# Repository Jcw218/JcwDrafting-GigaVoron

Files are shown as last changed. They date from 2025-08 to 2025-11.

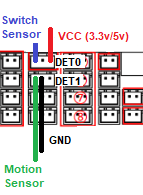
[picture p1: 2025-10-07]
BTT_smart_filament_detection_module_install_guide/filament detector.png

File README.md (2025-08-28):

# JcwDrafting-GigaVoron
Modifications to the Orangestorm Giga to improve its usability, Modifications and reliability. 
                                            WARNING!!! 
With the exception of the Print head; these modifications will not work with the original manufacturers motherboard or firmware.

Please be make sure you know the limits of your machine, the included data package is for the following parts:
- Octopus Pro V1.1 & V1.0 (F446 and H723)
- Raspberry Pi 4
- EB SB2209 CAN (RP2040 and STM32G0B1)
- BTT Eddy Duo (CANBUS Capable)
- BTT Pi V1.2
- Knomi 2 (important due to bed leveling integration. Bed level will not work without it. Modify the firmware to suit if it's not included)

To Install Klipper using the octopus pro as a CANBUS bridge follow Esoterical CANBUS guide here: https://canbus.esoterical.online/mainboard_flashing

Included in this data pacakge: 
- Apapter plate Step files for Stealth Burner and other hotend attachements
- Klipper install package to suit octopus pro, Raspberry pi, Eddy, BTT SB2209, SB2240, 
- Firmware for Octopus Pro and Raspbarry Pi motherboard upgrade
- Config for Octopus Pro motherboard upgrade and Stealthburner printer head
- Additional code and details for Obico Monitoring
- Adapter plate for nema 23 X axis upgrade
- Coming soon: Oem 10.1" TJC Touch Screen Firmware package for integration with new upgrades

Feel like buying me a coffee?

https://buymeacoffee.com/JakeCharles

bmc_qr

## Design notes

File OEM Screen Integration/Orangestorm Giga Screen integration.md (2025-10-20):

####################################################################################
### Machine type: JcwGiga
### Current configuration version: VBeta
### Date：2025-10-20
### OEM SCREEN INTEGRATION WITH OPEN SOURCE KLIPPER INSTALL
### OEM Stepper Motors and Stock Stepper Drivers
####################################################################################

This is a guide on how to configure the OEM SCREEN to operate with new board hardware running a newer version of klipper. This being said, this guide can also be applied to newer versions of klipper installed on the OEM board running a MKS pi

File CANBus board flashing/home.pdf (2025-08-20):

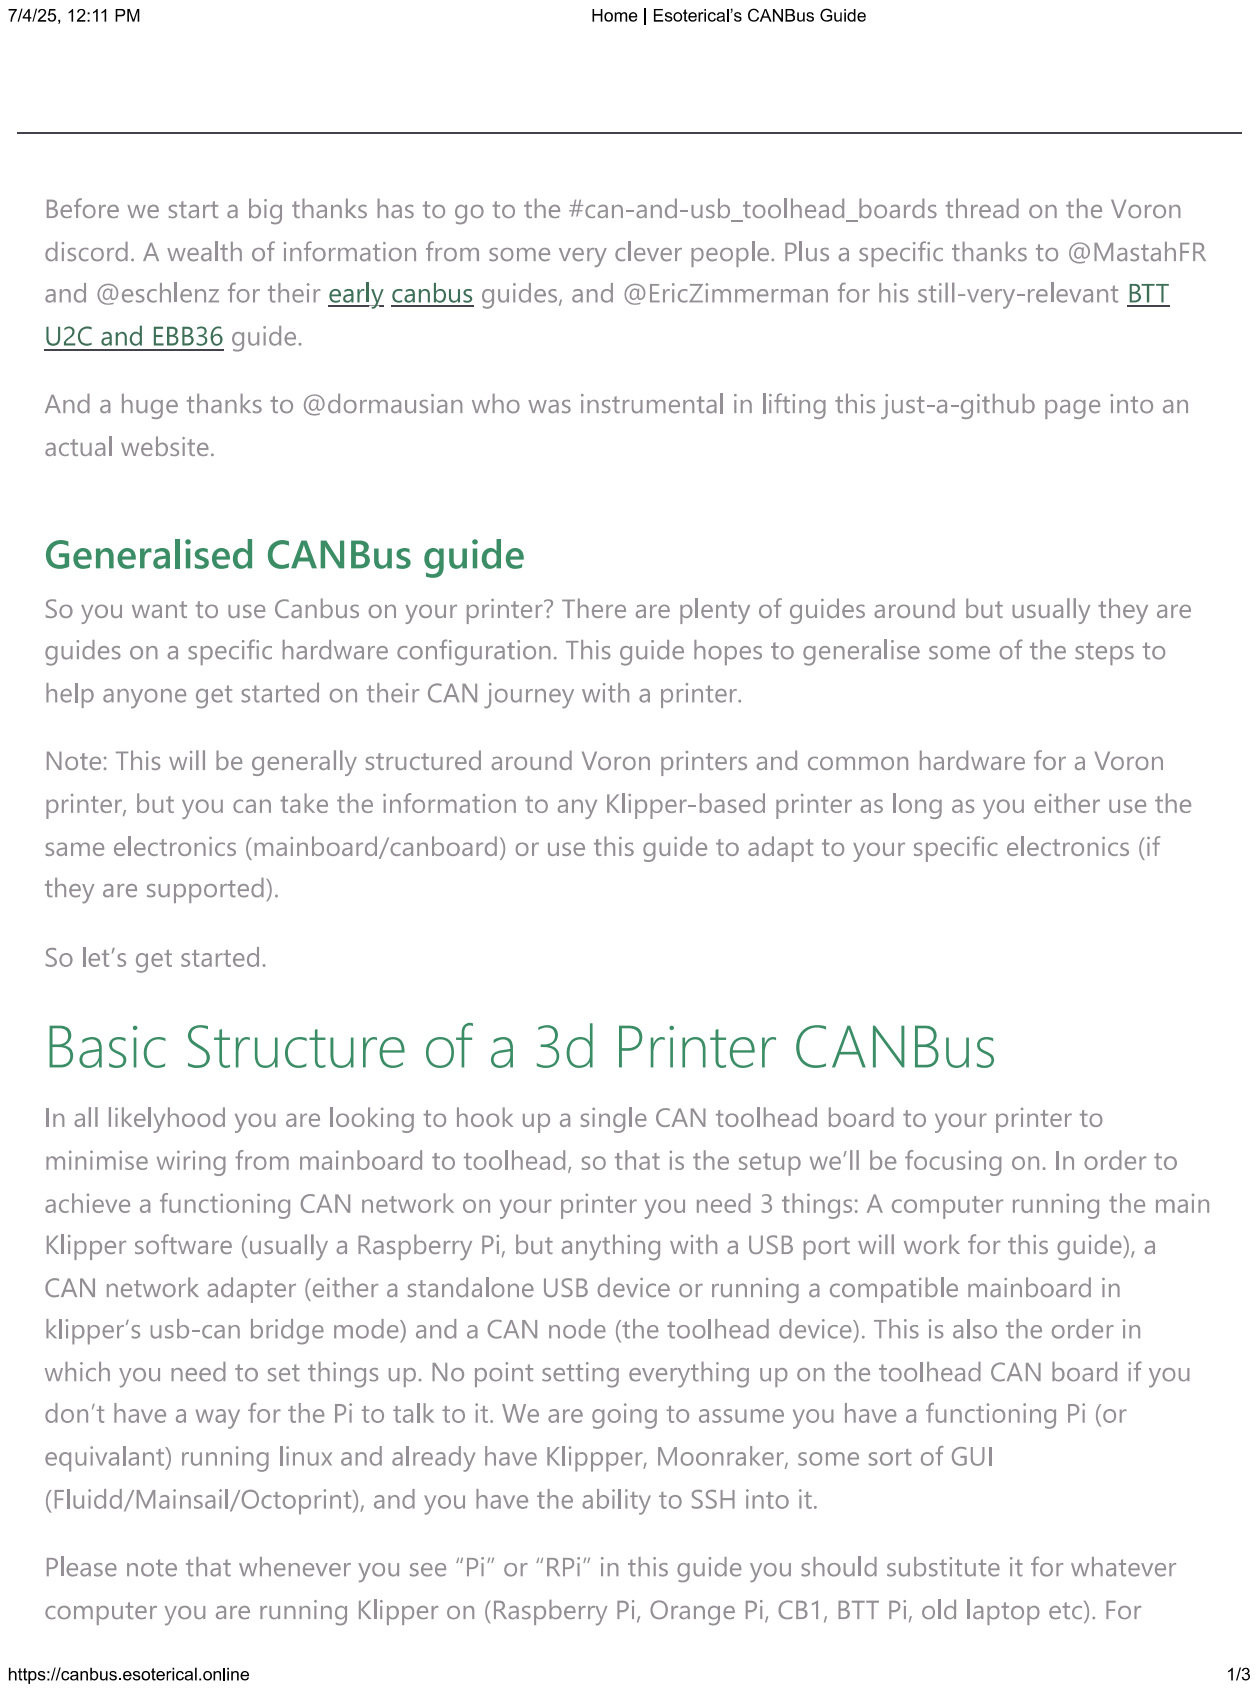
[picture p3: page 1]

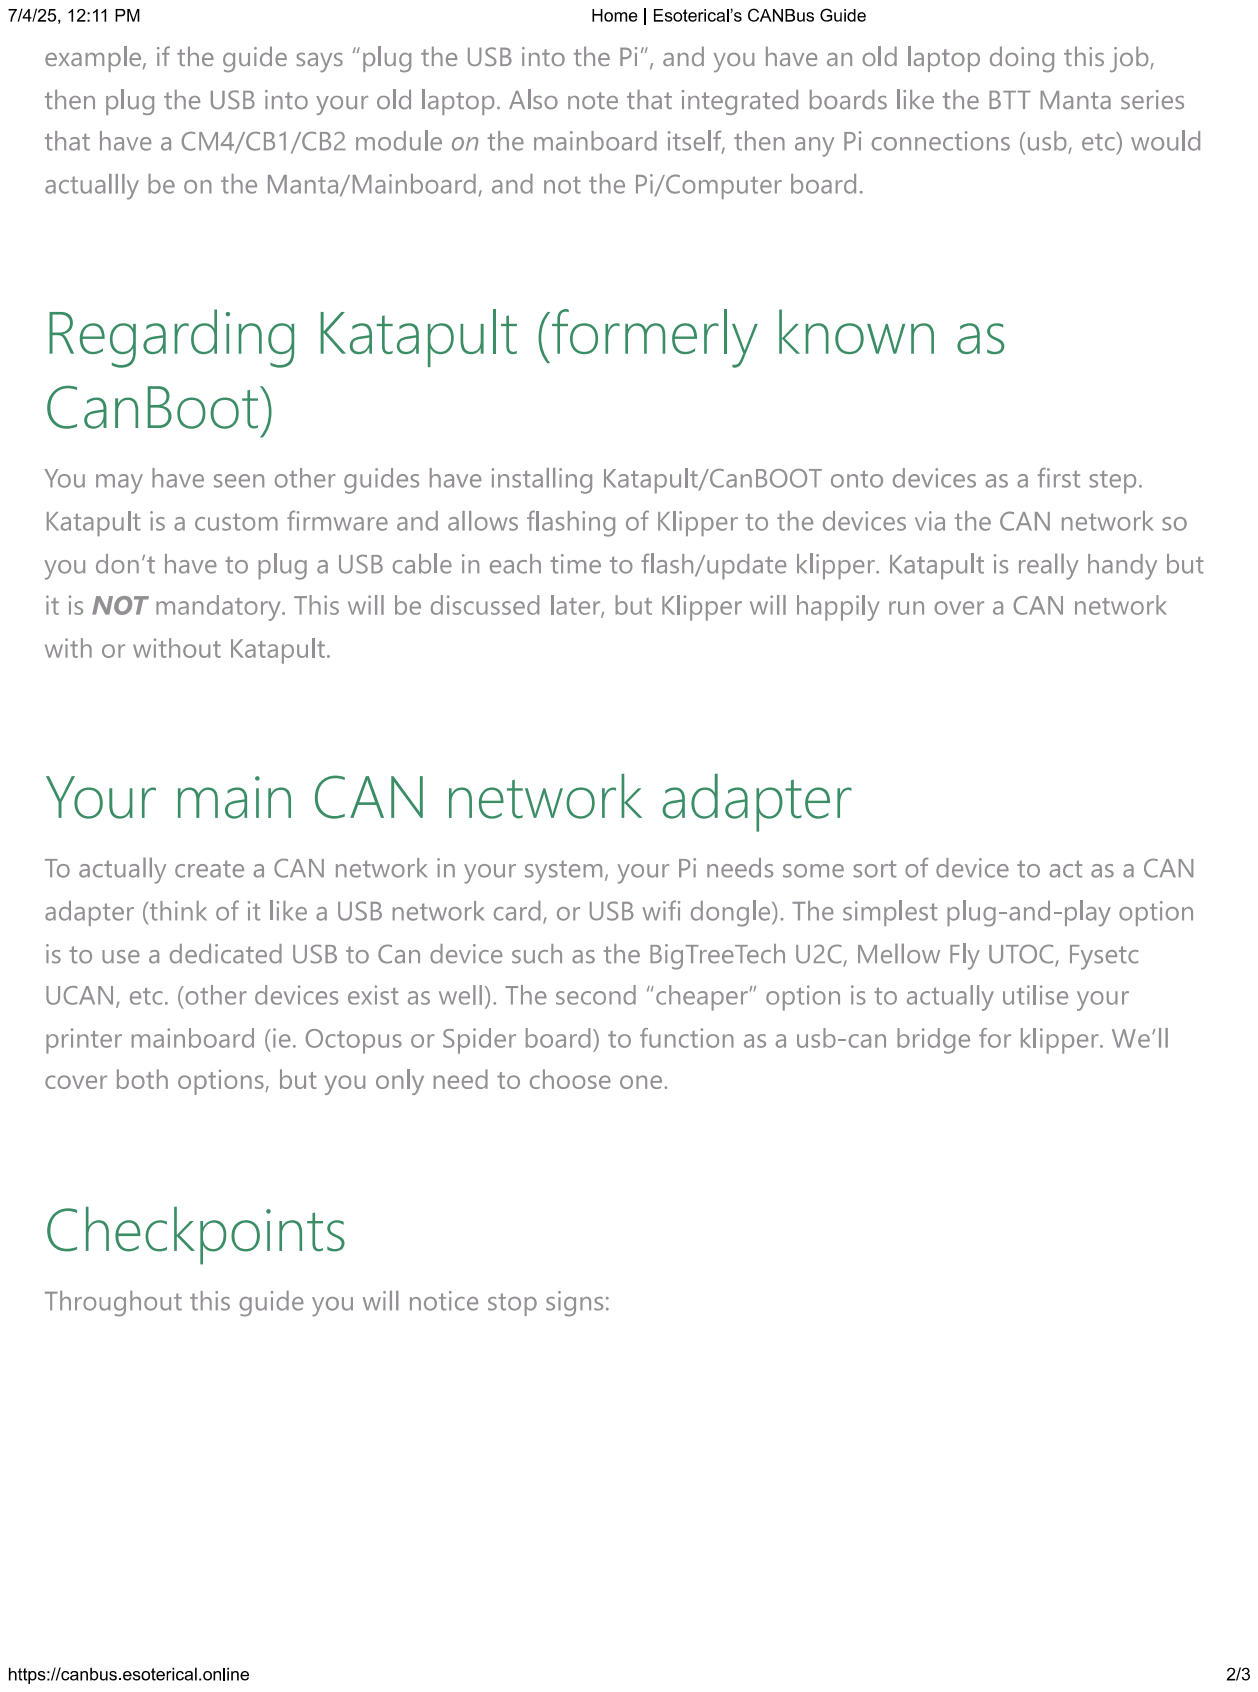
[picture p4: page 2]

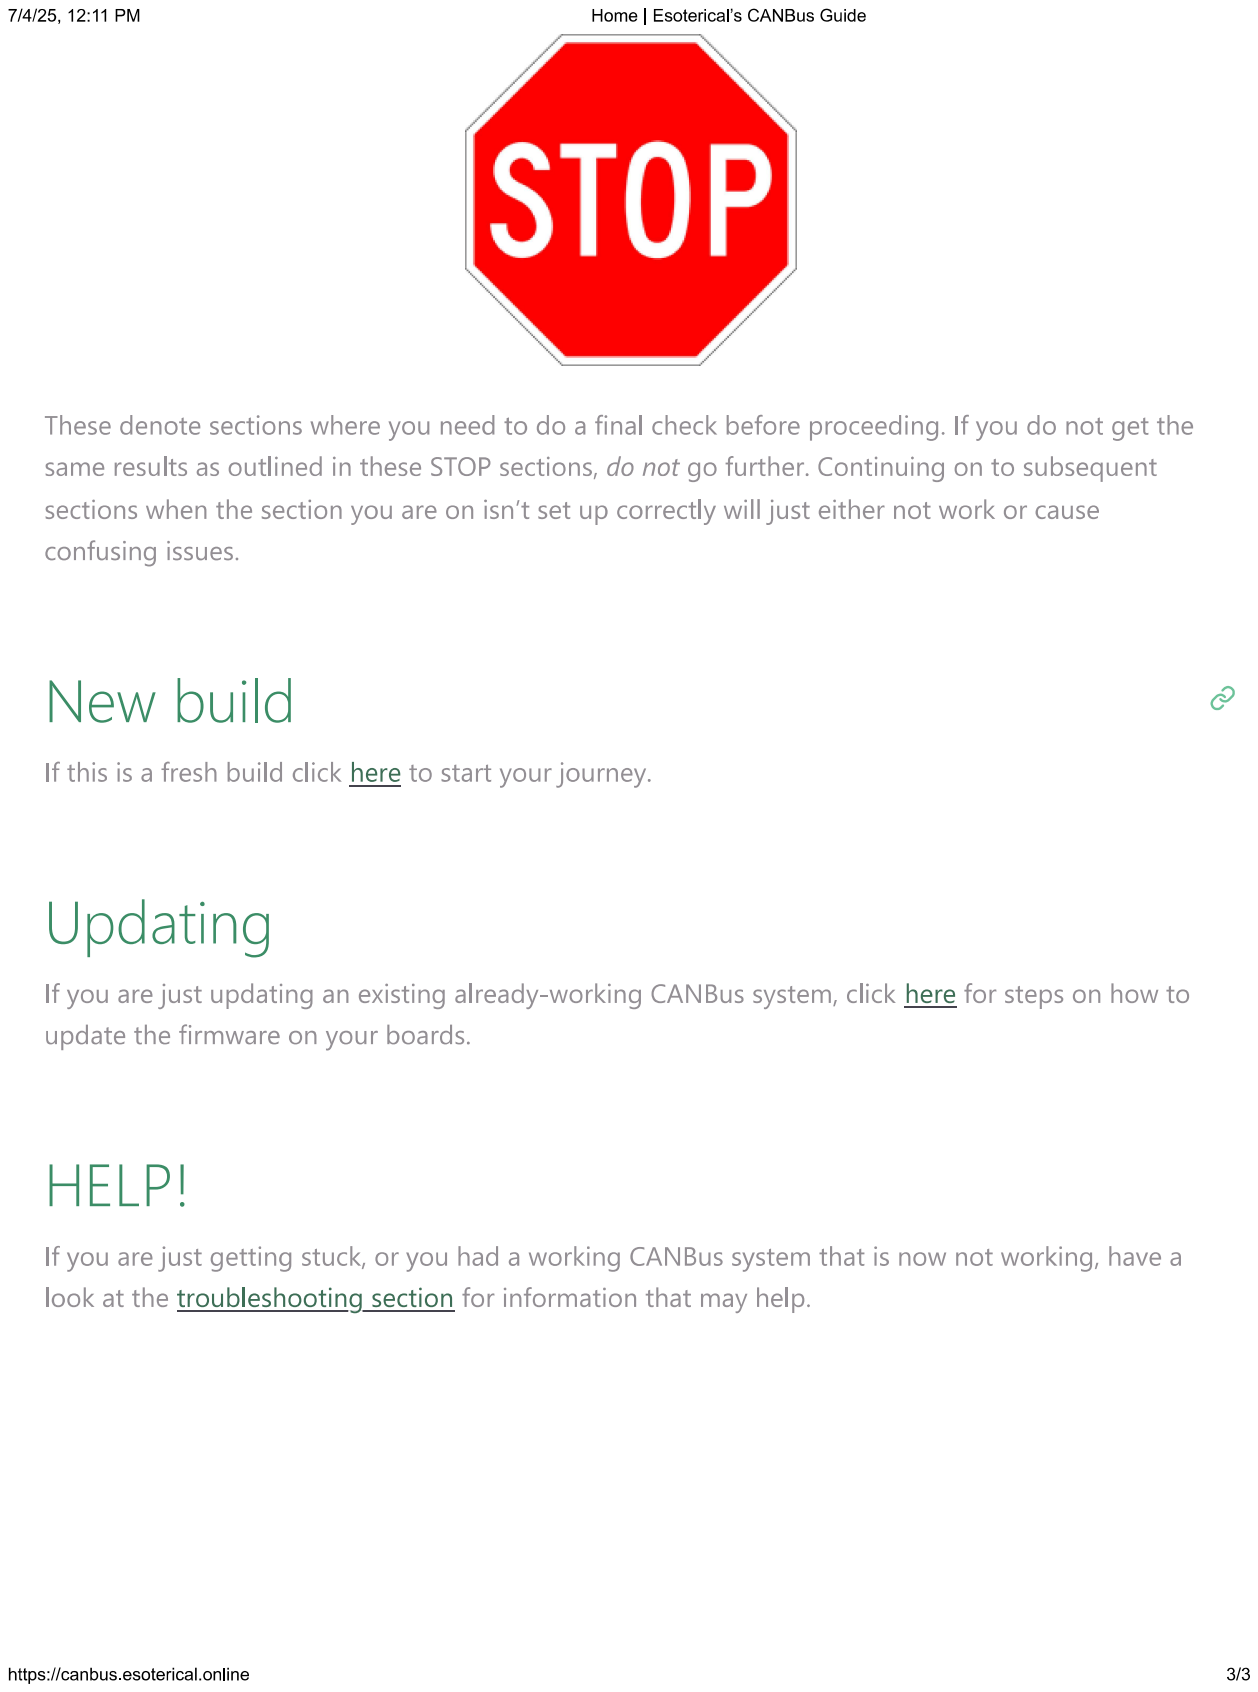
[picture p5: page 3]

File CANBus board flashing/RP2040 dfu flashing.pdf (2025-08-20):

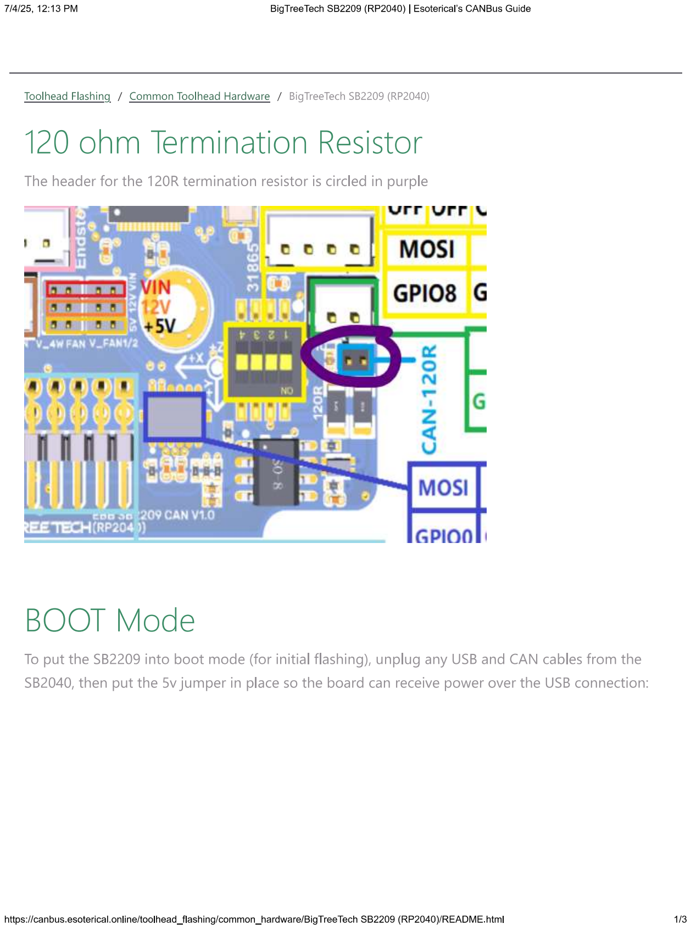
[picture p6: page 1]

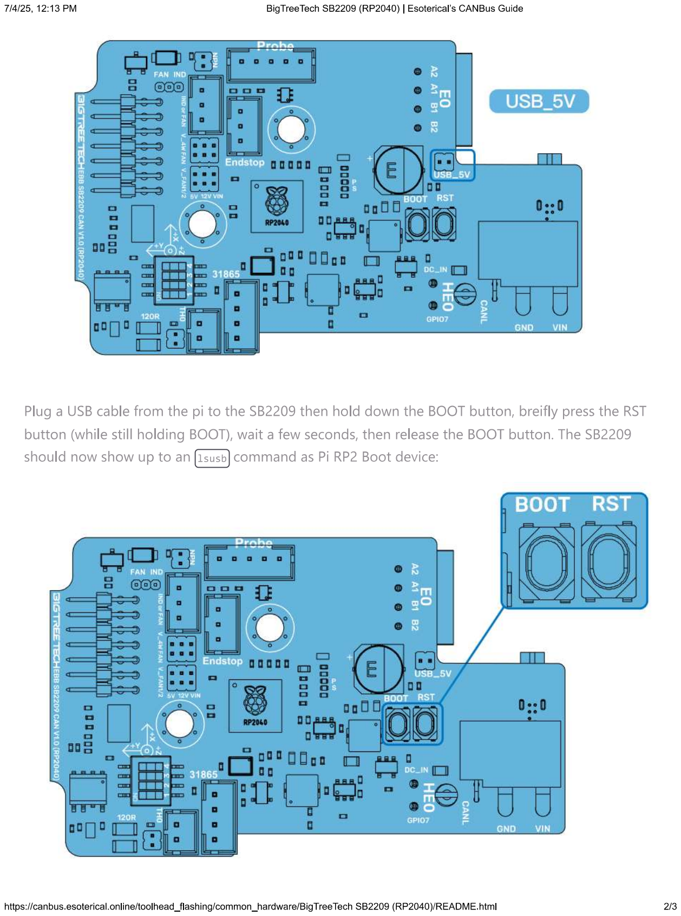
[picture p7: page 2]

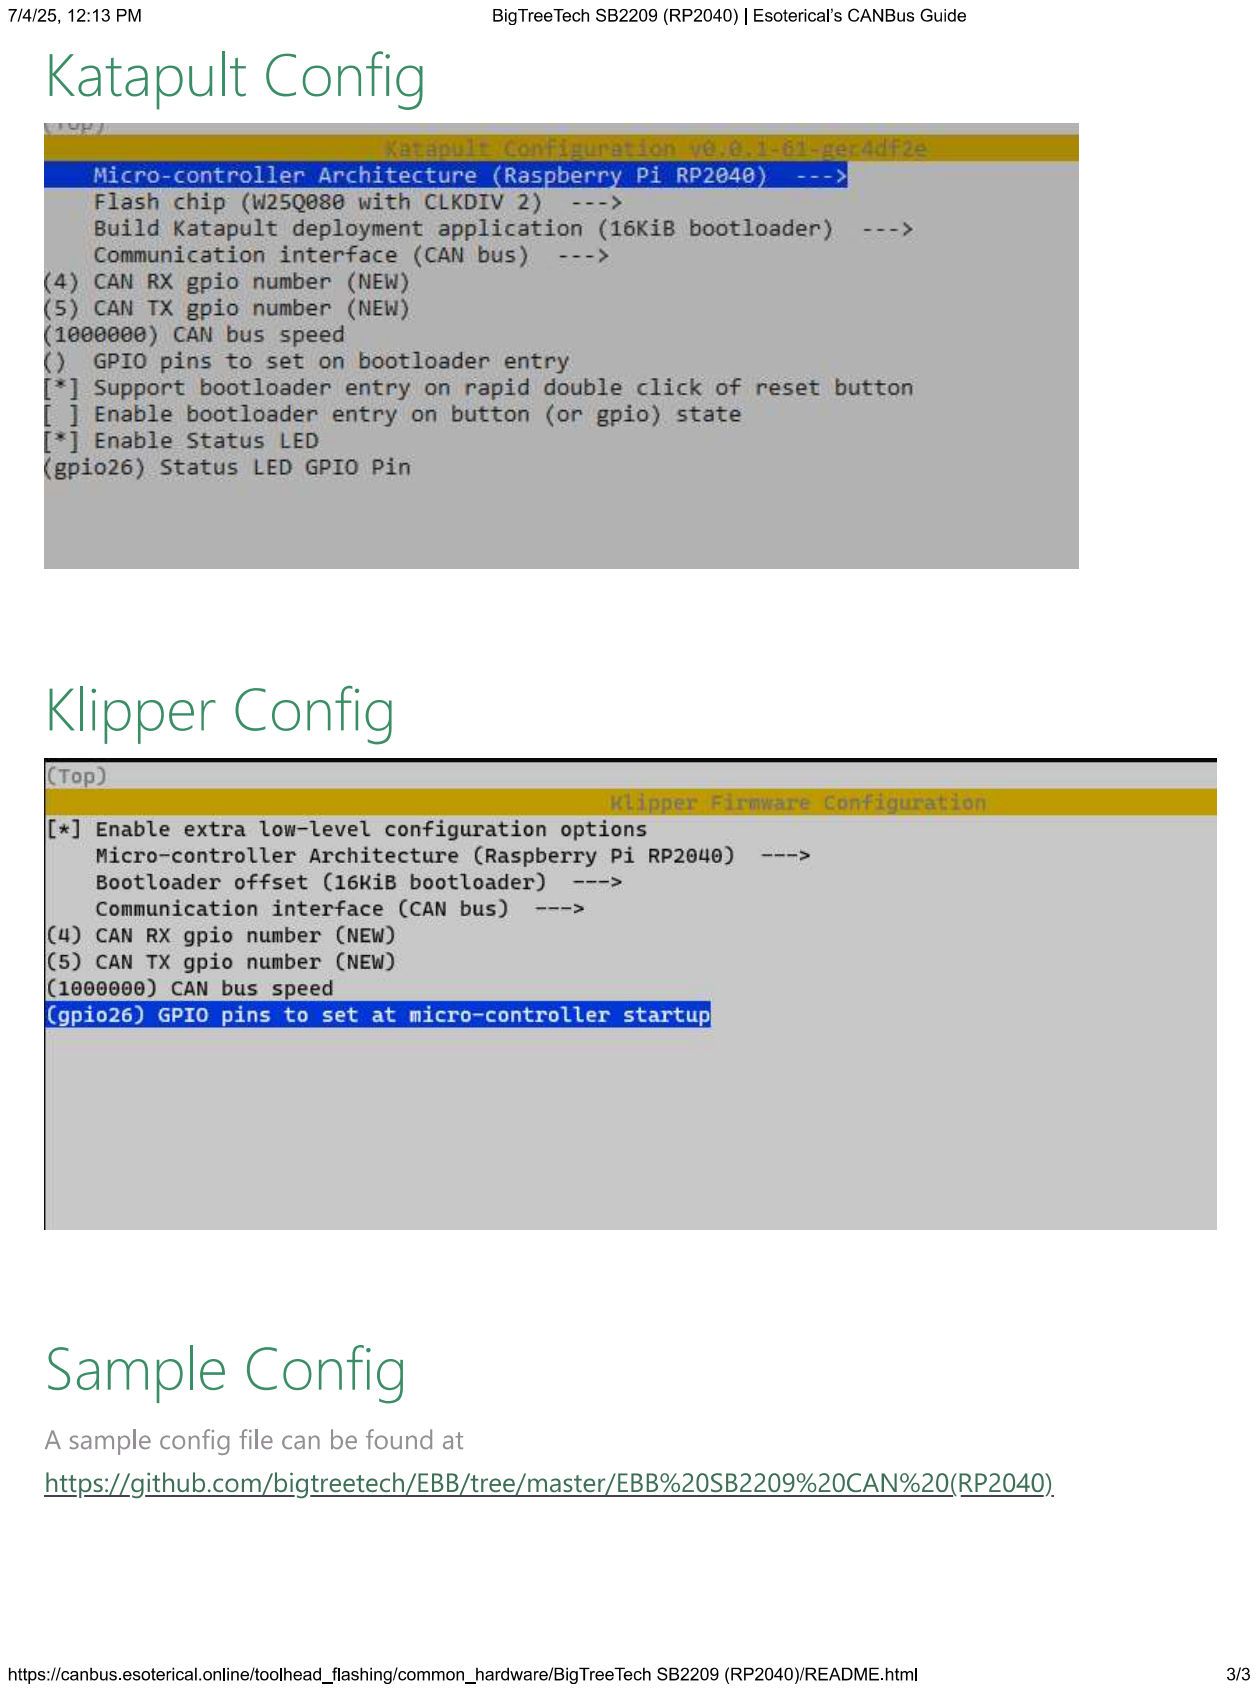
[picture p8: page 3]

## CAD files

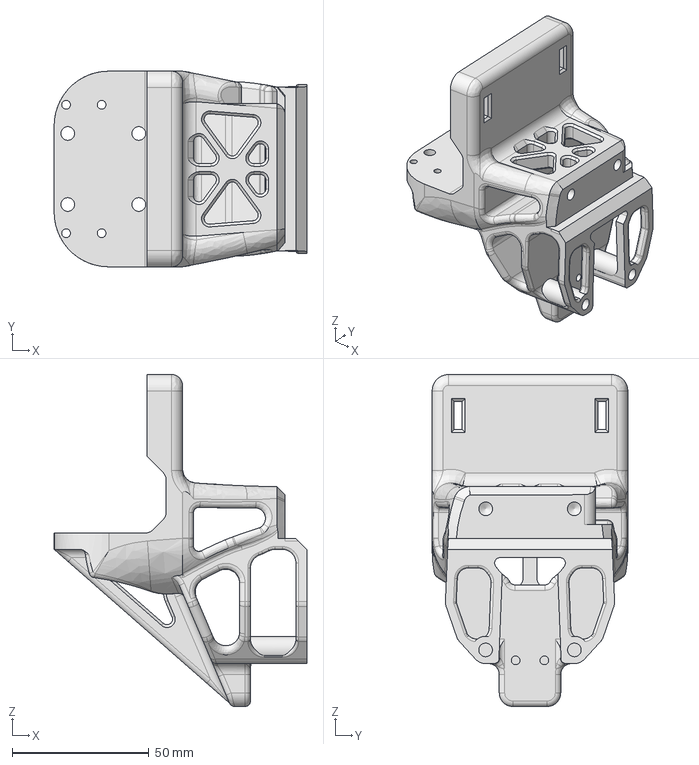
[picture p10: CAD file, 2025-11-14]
3D Print File - Dragon ACE SB with Extension/Full Printhead unit.stp
92.5 x 71.6 x 121.5 mm

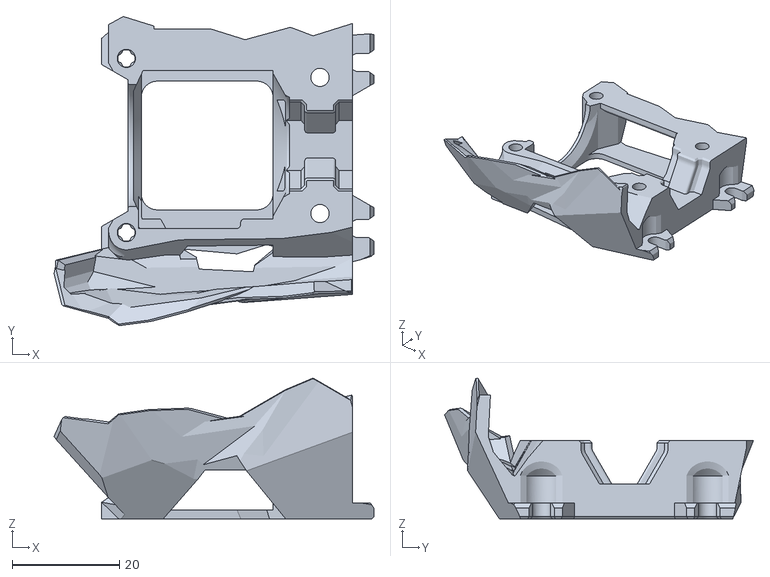
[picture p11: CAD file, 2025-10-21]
3D Print File - Bambulabs SB/BambuLabs SB Back.stl
59.7 x 57.7 x 26.3

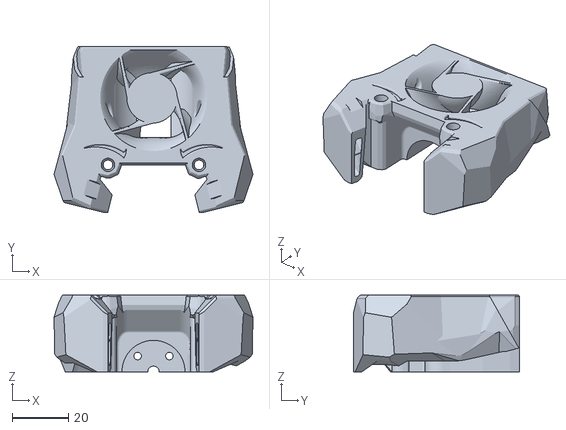
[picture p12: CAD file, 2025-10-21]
3D Print File - Dragon Ace SB/Dragon ACE SB Front.stl
71.1 x 59.1 x 27.4

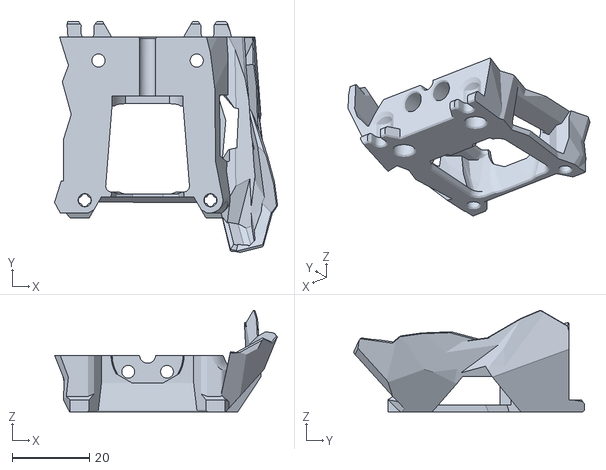
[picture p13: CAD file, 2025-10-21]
3D Print File - E3D Revo SB/E3D Revo SB Back.stl
57.7 x 59.7 x 26.3

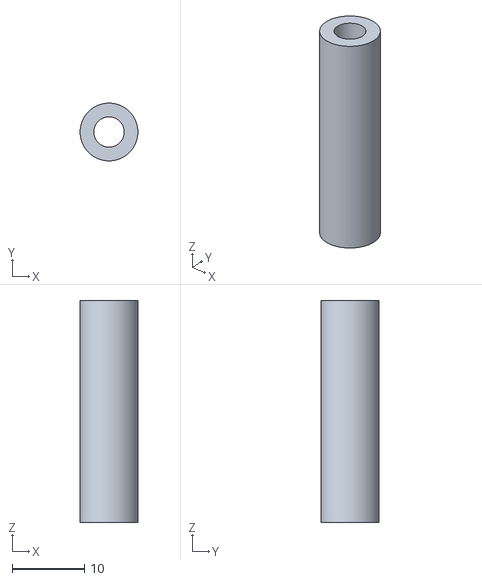
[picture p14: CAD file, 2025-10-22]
3D Print File - Giga Modifications/Bed Leveling Bushes.stl
8.00 x 8.00 x 30.7

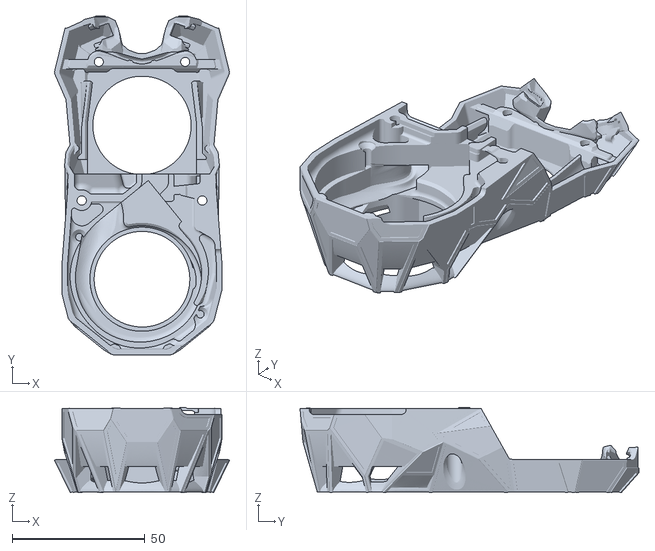
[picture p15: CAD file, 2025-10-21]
3D Print File - SB Components/Jcw Drafting Stealth Burner Face.stl
66.0 x 127.7 x 32.1

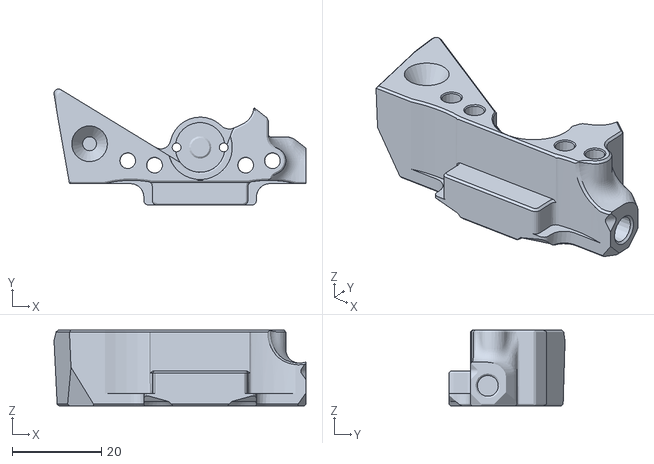
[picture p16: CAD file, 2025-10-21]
3D Print File - SB Galileo V2/SB Galileo Base Hinge Retainer.stl
56.4 x 26.0 x 17.0

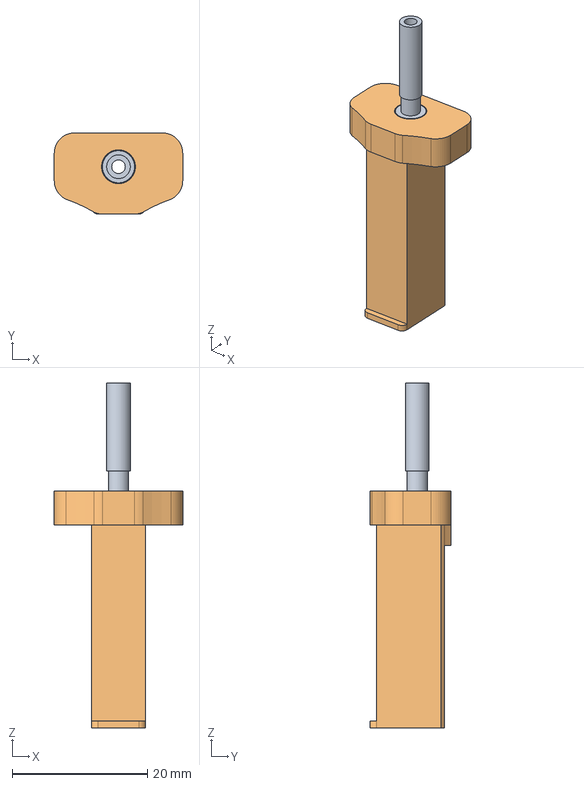
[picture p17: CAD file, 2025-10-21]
Stock Giga Print Head 3D models/Giga Extruder hotend.stp
19.0 x 12.0 x 51.0 mm

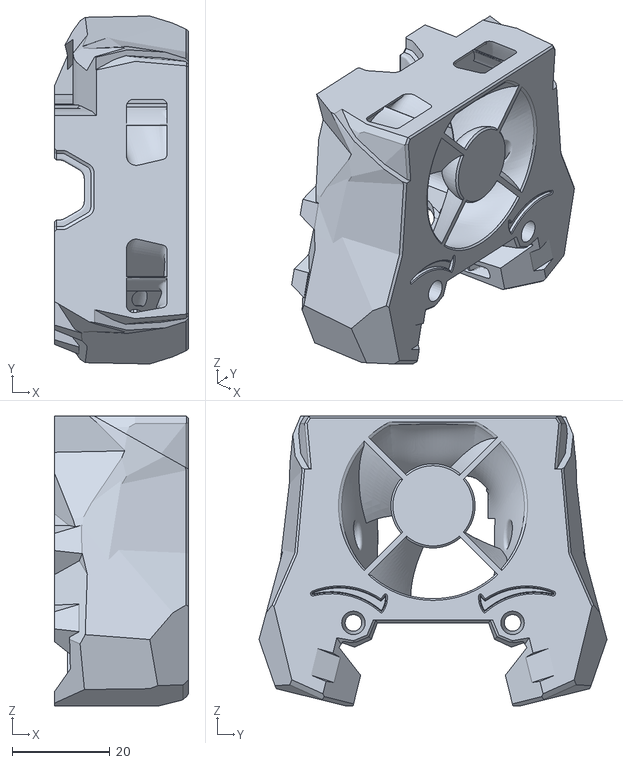
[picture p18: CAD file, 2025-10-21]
3D Print File - Bambulabs SB/Bambulab SB Front.stl
27.4 x 71.1 x 59.1

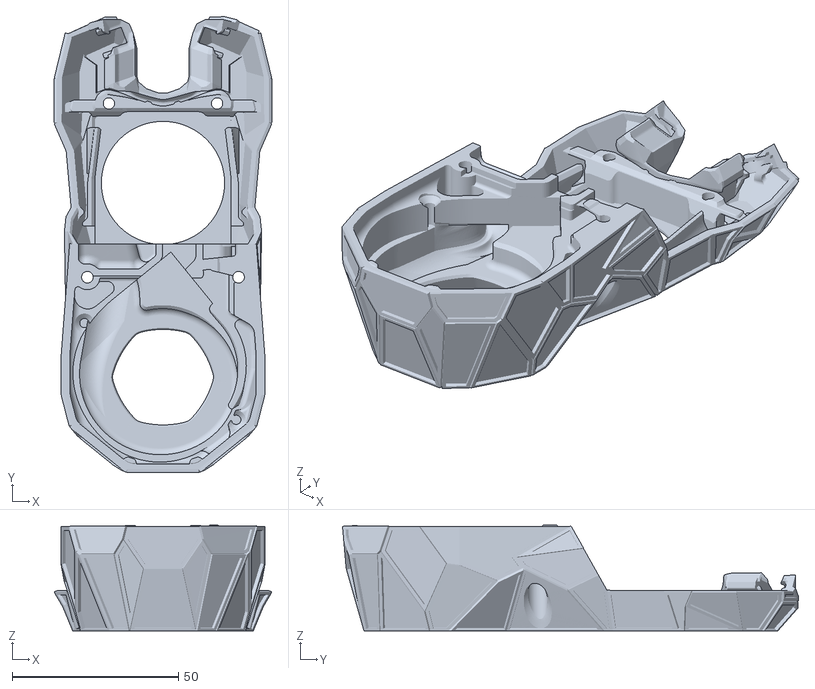
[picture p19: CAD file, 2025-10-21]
3D Print File - Dragon ACE SB with Extension/Dragon Ace SB with Extension Face.stl
65.3 x 137.0 x 31.8

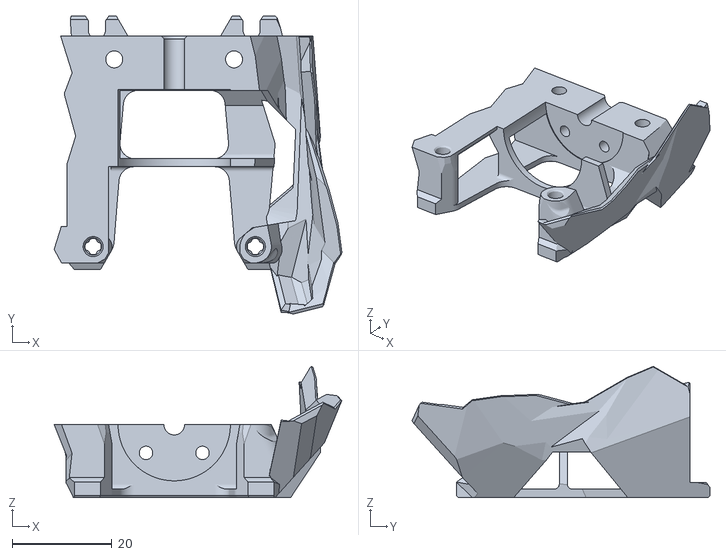
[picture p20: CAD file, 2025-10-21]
3D Print File - Dragon Ace SB/Dragon ACE SB Back.stl
57.7 x 59.7 x 26.3

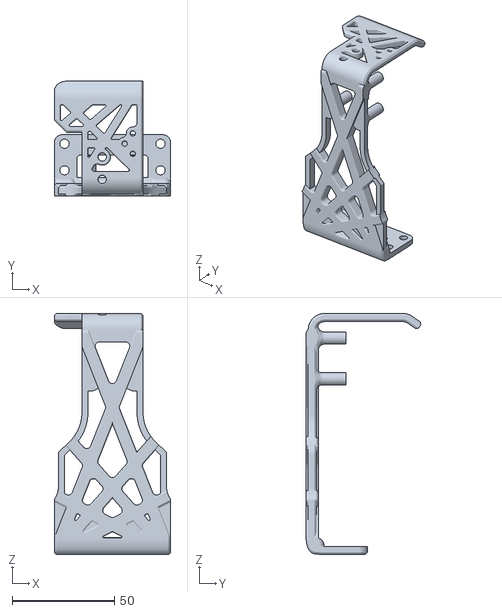
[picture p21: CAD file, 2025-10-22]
3D Print File - Giga Modifications/Giga Extruder Canbus cable chain bracket.stl
57.0 x 56.2 x 118.0

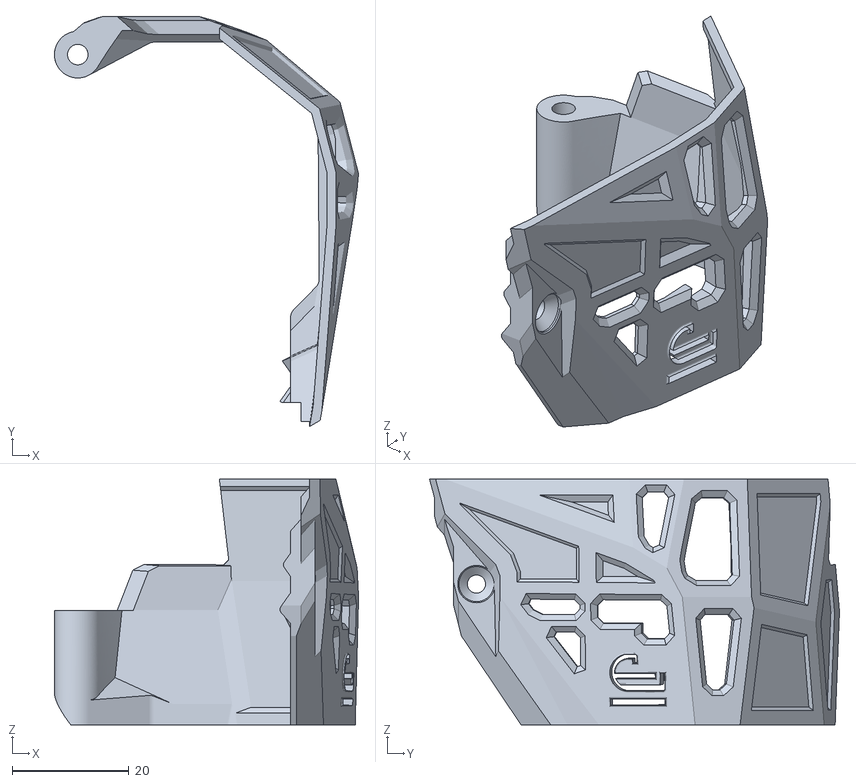
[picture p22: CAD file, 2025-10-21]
3D Print File - SB Components/SB Electronics Shroud.stl
52.1 x 70.2 x 42.1

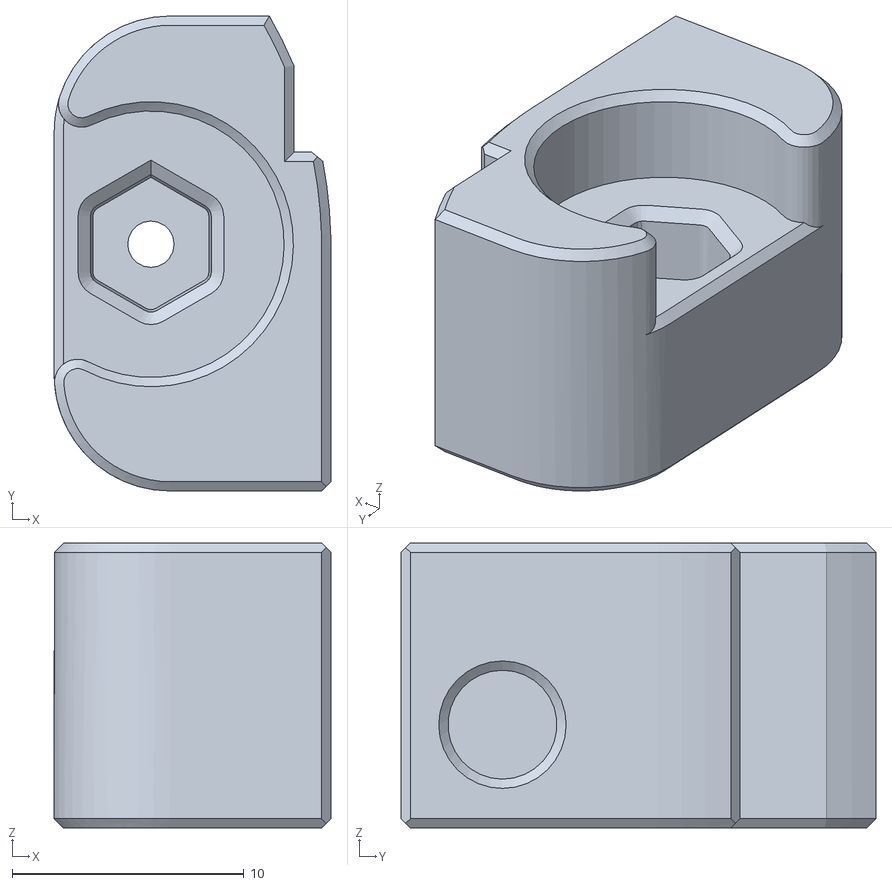
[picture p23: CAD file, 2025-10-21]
3D Print File - SB Galileo V2/SB Galileo Extruder Bearing Retainer.stl
11.9 x 20.5 x 12.3

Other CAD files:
3D Print File - OG Dragon SB/Dragon SB Back.stl
3D Print File - E3D Revo SB/E3D Revo SB Front.stl
3D Print File - OG Dragon SB/Dragon SB Front.stl
Stock Giga Print Head 3D models/Level Sensor v3.stp
3D Print File - Bambulabs SB/BambuLabs SB Adapter.stl
3D Print File - Dragon ACE SB with Extension/Dragon ACE SB with Extension Back.stl
3D Print File - Dragon ACE SB with Extension/Dragon ACE SB with Extension Front.stl
3D Print File - Giga Modifications/Giga Extruder Linear Rail Plate.stl
3D Print File - Giga Modifications/Giga Frame Corner Brace with enclosure mount hole.stl
3D Print File - Giga Modifications/Giga Z axis Bushing for Calibration.stl
3D Print File - Giga Modifications/Nema17 to Nema23 x axis adapter.stl
3D Print File - Giga Modifications/Octopus Pro Motherboard Mounting bracket.stl
3D Print File - Giga Modifications/PI Mouting bracket.stl
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

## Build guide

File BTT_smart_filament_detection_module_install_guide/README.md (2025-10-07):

## Guide to Installing the BTT smart filament detection module to the original Elegoo Orangestorm Giga Motherboard V3
558768329_10235050453376534_4001759081982270624_n

1. Firslty, figure out where you want the sensor. If the sensor is too far away from the print head, it may trigger more regularly than if the sensor was placed closer to the print head.


2. If you are using the DET0 and DET1 headers at the back of the printer; make sure both headers are properly pluged into the headers on the motherboard. You may need to run another cable from the DET1 header to the DET1 on the motherboard.

  558884123_10235066154769059_1636835637515836587_n
  557631873_10235066176769609_8913204024433743418_n

4. The BTT smart filament sensor should be wired as per the following image:
  filament detector

5. Locate the IP address of your printer.
  

6. Enter the IP address of your printer into google chrome and hit enter. You'll be greeted by the Fluidd Interface.
  

7. Locate the Configuration tab on the left side of the Interface.
  

8. Double left click on the printer.cfg file

9. scroll down and find the following entry.
  

10. type # to uncomment this code or delete this code and then type in the following instead:
  

11. PD5 is the incorrect swtich_pin id. located you pins.h file and determine the right ID to enter in the place of PD5. The encorder pin detects if the filament is running through the switch and is very handy to determine whether your first layer is accurate or whether you have a clogged nozzle.

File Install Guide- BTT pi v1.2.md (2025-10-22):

####################################################################################
### Machine type: JcwGiga
### Current configuration version: VBeta
### Date：2025-9-11
### BTT Pi V1.2 - Octopus pro V1.1 - EBB SB2209-RP2040
### OEM Stepper Motors and Stock Stepper Drivers
####################################################################################

This is a Tutorial on how to install this repositories operating system to a BTT pi V1.2 and configure it for the Elegoo Orangestorm Giga manually

Step 1:
Ensure that your Giga is turned off and isolated from power. You may also want to wait a day to ensure that the capacitors are drained of electricity and are safe to touch.

Step 2:
Removing the Mother board cover panel on the right side of the machine as detailed in the images below:

  - Ensure that your print head is at the z heigth of 300-500 and out of the way so that the motherboard panel can be removed. You may need to manually home first and then set the z height to 300 or 500.
    
    
    
  - Loosen the 2 screws fixed by the PEI limit block at the right front and back side of the printer using a 2.0mm Allen wrench to remove the PEI limit block.
    
    
  
  - Disconnect the ribbon cables from the rear adapter board located on the right side of the printer.
    
    
  
  - Use a 2.0mm Allen wrench to loosen the 8 screws securing the power supply cover.
    
    

  - Slide the power supply cover downward towards the heated bed, then lift the outer edge of the cover to remove it.
    
    

Step 3:
Removing the Motherboard and marking the wires as per the images below:

  - Use cable ties or label paper to mark the ribbon cables that lack original markings, ensuring they correspond to the port names on the motherboard.
    
    

    Motherboard sch

  - Disconnect all ribbon cables from the ports on the motherboard. Use a 2.0mm Allen wrench to loosen the 4 screws securing the motherboard, and remove the old motherboard.

    

Step 4:
Install Klipper onto Big Tree Tech pi V1.2, Octopus Pro V1.1 and the Big tree tech boards EBB SB2209 and the BTT Eddy

  - Download Raspberry pi imager: https://downloads.raspberrypi.com/imager/imager_latest.exe

    raspberry pi imager

  - Download the latest BTT CB1 pi image (CB1_Debian12_minimal_kernel6.6_20241219.img.xz) here: https://github.com/bigtreetech/CB1/releases

   CB1 image

  - Insert a spare micro SD card into your computer, preferably of a 32-64gb storage size.

  - Open Raspberry pi imager, input the following settings: Raspberry Pi Devices: No Filtering, Operating system: (Use custom)CB1_Debian12_minimal_kernel6.6_20241219.img.xz, Storage:GENERIC MASSSTORAGECLASS USB Device - 32-64gb SD card

    raspberry pi imager settings

  - Hit next than edit settings with your wireless LAN name, password, Set username and password to user: biqu password: biqu, Set hostname to Jcwgiga.local and ensure your wireless LAN country is selected, time zone and keyboard is correct.

  - Next select the Services tab and enable SSH and Use password authentication. After this hit save and then YES to start the writing process. It may take a few minutes.

  - Once complete, open "This PC" (if using windows), select the boot partition of the sd card and open the system.cfg file.
     - Remove the # from hostname and input: "Jcwgiga" instead of "BIGTREETECH-CB1"
     - change the wifi settings to match your wifi settings.
     - hit save and close

      btt config setting
       
  - Next open the armbianEnv.txt file located in the same folder
     - Change console=display to equal console=serial
     - hit save and close

      ArmbianEnv

  - Take out the SD card and insert it into the BTT pi. Plug the Usb C cable from the BTT pi v1.2 into the computer ensuring that the black jumper clip is installed as per the image:

    BTT PI

  - Either wait for the wifi to connect or plug in an RJ45 Ethernet cable for internet access.

  - Download and install putty: https://www.chiark.greenend.org.uk/~sgtatham/putty/latest.html

  - Open putty and enter in Jcwgiga.local (or whatever you'd like to set it as) as the Host Name (or IP address), connection type is SSH and port is 22

    putty

  - You will be prompted for a username and password. Enter in biqu for username and for password: biqu. don't worry if the password doesn't show on the screen, it's hidden from view by default.

  - Next is the intimidating coding portion of this build. (follow esoterical guide for installing klipper in CANBus bridge mode: https://canbus.esoterical.online/mainboard_flashing)

    - In order to create the CAN network, copy and paste the next line of code into putty:

      uname -a

    - next copy and paste the next line of code and right click anywhere in putty. hit enter:

      sudo systemctl enable systemd-networkd

    - Then copy and paste the next line of code and right click anywhere in putty. hit enter:
   
      sudo systemctl start systemd-networkd

    - Next check that the service is running by copying and pasting the next line of code in putty. hit enter:
   
      systemctl | grep systemd-networkd

      396017770-901096ef-29c8-4abc-8191-8d6c6aec9010

    - Next copy the next line of code and right click anywhere in putty. hit enter:

      sudo systemctl disable systemd-networkd-wait-online.service

    - Next copy the next line of code and right click anywhere in putty. hit enter:
   
      echo -e 'SUBSYSTEM=="net", ACTION=="change|add", KERNEL=="can*"  ATTR{tx_queue_len}="128"' | sudo tee /etc/udev/rules.d/10-can.rules > /dev/null

    - Next copy the next line of code and right click anywhere in putty. hit enter:
   
      cat /etc/udev/rules.d/10-can.rules

    - the response should look like this:

      

    - Next copy the next line of code and right click anywhere in putty. hit enter:
   
      echo -e "[Match]\nName=can*\n\n[CAN]\nBitRate=1M\n\n[Link]\nRequiredForOnline=no" | sudo tee /etc/systemd/network/25-can.network > /dev/null

    - Next copy the next line of code and right click anywhere in putty. hit enter:

      cat /etc/systemd/network/25-can.network

    - it should look like this:

      

    - Finally restart the pi by copying the next line of code and right clicking anywhere in putty. hit enter:

      sudo reboot now

    - There's a deviation at this point regarding your setup. These next steps explain the config for 1 octopus pro running in canbus bridge mode with a btt pi v1.2. Different installs 
    
    - copy this next code and right click anywhere on the putty program:
      
      sudo apt update
      
      sudo apt upgrade
      
      sudo apt install python3 python3-serial

      If you get an error along the lines of “unable to locate package python3-serial” then you may be on an older version of linux.

      In that case, run:

      sudo apt install python3-pip

      then

      pip3 install pyserial

    - copy this next code and right click anywhere in putty to paste, then hit enter.
   
      test -e ~/katapult && (cd ~/katapult && git pull) || (cd ~ && git clone https://github.com/Arksine/katapult) ; cd ~

    - copy this next code and right click anywhere in putty to paste, then hit enter.
   
      cd ~/katapult
      
      make menuconfig

    - you'll then be greeted with the klipperconfig screen. locate your motherboard config settings here and fill in the right values for your board: https://canbus.esoterical.online/mainboard_flashing/common_hardware.html
    
      301052290-5434691f-2d97-4d75-9067-d7501c2a2214
    
    - press q to quit and save the config. then copy this code and right click anywhere in putty and press enter.
   
      make clean
      
      make

    - To flash, connect your mainboard to the Pi via USB then put the mainboard into DFU/BOOT mode (your mainboard user manual should have instructions on doing this).

      If your mainboard board uses an STM32 based MCU use these flashing steps: https://canbus.esoterical.online/mainboard_flashing.html#stm32-based-boards

      If your mainboard board uses an RP2040 MCU, use these flashing steps: https://canbus.esoterical.online/mainboard_flashing.html#rp2040-based-boards

    - next copy this code and enter it into putty. you should see your board listed and in DFU mode:

      lsusb

    - next copy and paste this code into putty. Please note that the 8 digits at the end of this code will be the same as your board digits as listed in the previous step.
   
      cd ~/katapult
      
      make
      
      sudo dfu-util -R -a 0 -s 0x08000000:mass-erase:force:leave -D ~/katapult/out/katapult.bin -d 0483:df11

     - next take your motherboard out of DFU mode. This could be a jumper plug or similar. it may already be out of DFU mode, in which case proceed to the following step.
     - 
     - next copy the next line of code and right click anywhere in putty:
       
       ls /dev/serial/by-id

    - Take note of the next response that putty gives you, screen shot this code, right it down, record it somewhere and don't lose it. The response should look like this:
   
       
    
    - 
      
    - copy this and right click anywhere on the putty program:
      
       ./kiauh/kiauh.sh
      
    - Select Y to keep kiauh up to date.
      
    - Enter the previous command in again:
      
      ./kiauh/kiauh.sh
      
    - type "4" for no and remeber my choice
      
    - type "1" for install ENTER
      
    - (OPTIONAL INSTALL) type "9" for obico ENTER
      
    - (OPTIONAL CONFIG) run through the process of setting up your obico account and link it by using the code or the search function in the phone app
      
    - type "B" for back ENTER
      
    - type "2" for update ENTER
      
    - type "a" Update all ENTER
      
    - if prompted for anything type ENTER for the default option
  
  - Install Octopus Pro Adapter Bracket using the same 4 screws.

  - Plug in the cables to the octopus pro using the following schematic.

    Octopus pro wiring schematic (GIGA) (OEM)

    - UART_NOTE 1: Pull the black Jumper clips from the octopus pro board to match the following SPI Diagram.
      
      Octopus pro UART

    - STEPPER_NOTE 2: Pull the Black Jumper clips from the ocotopus pro board and place them back to match the following STEPPER Diagram.

      

    - FAN_POW NOTE 3: Pull the Black Jumper Clips from the octopus pro board and place them back to match the following FAN POW Diagram.

      FAN POW

  -

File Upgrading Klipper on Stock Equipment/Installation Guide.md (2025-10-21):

####################################################################################
Machine type: Elegoo Orangestorm Giga
Current configuration version: OPENSOURCE Klipper
Date：2025-10-21
Elegoo V3.0 Makersbase Rockchip rk3328 board with emmc mks pi or emmc Giga pi
All Stock Equipment, simply installing open source klipper for better support and equipment integration.
####################################################################################

The Following guide is for the install of open source klipper on the Elegoo Orangestorm giga stock equipment, I'm not talking about v12, I mean direct updates using kiauh or similar.

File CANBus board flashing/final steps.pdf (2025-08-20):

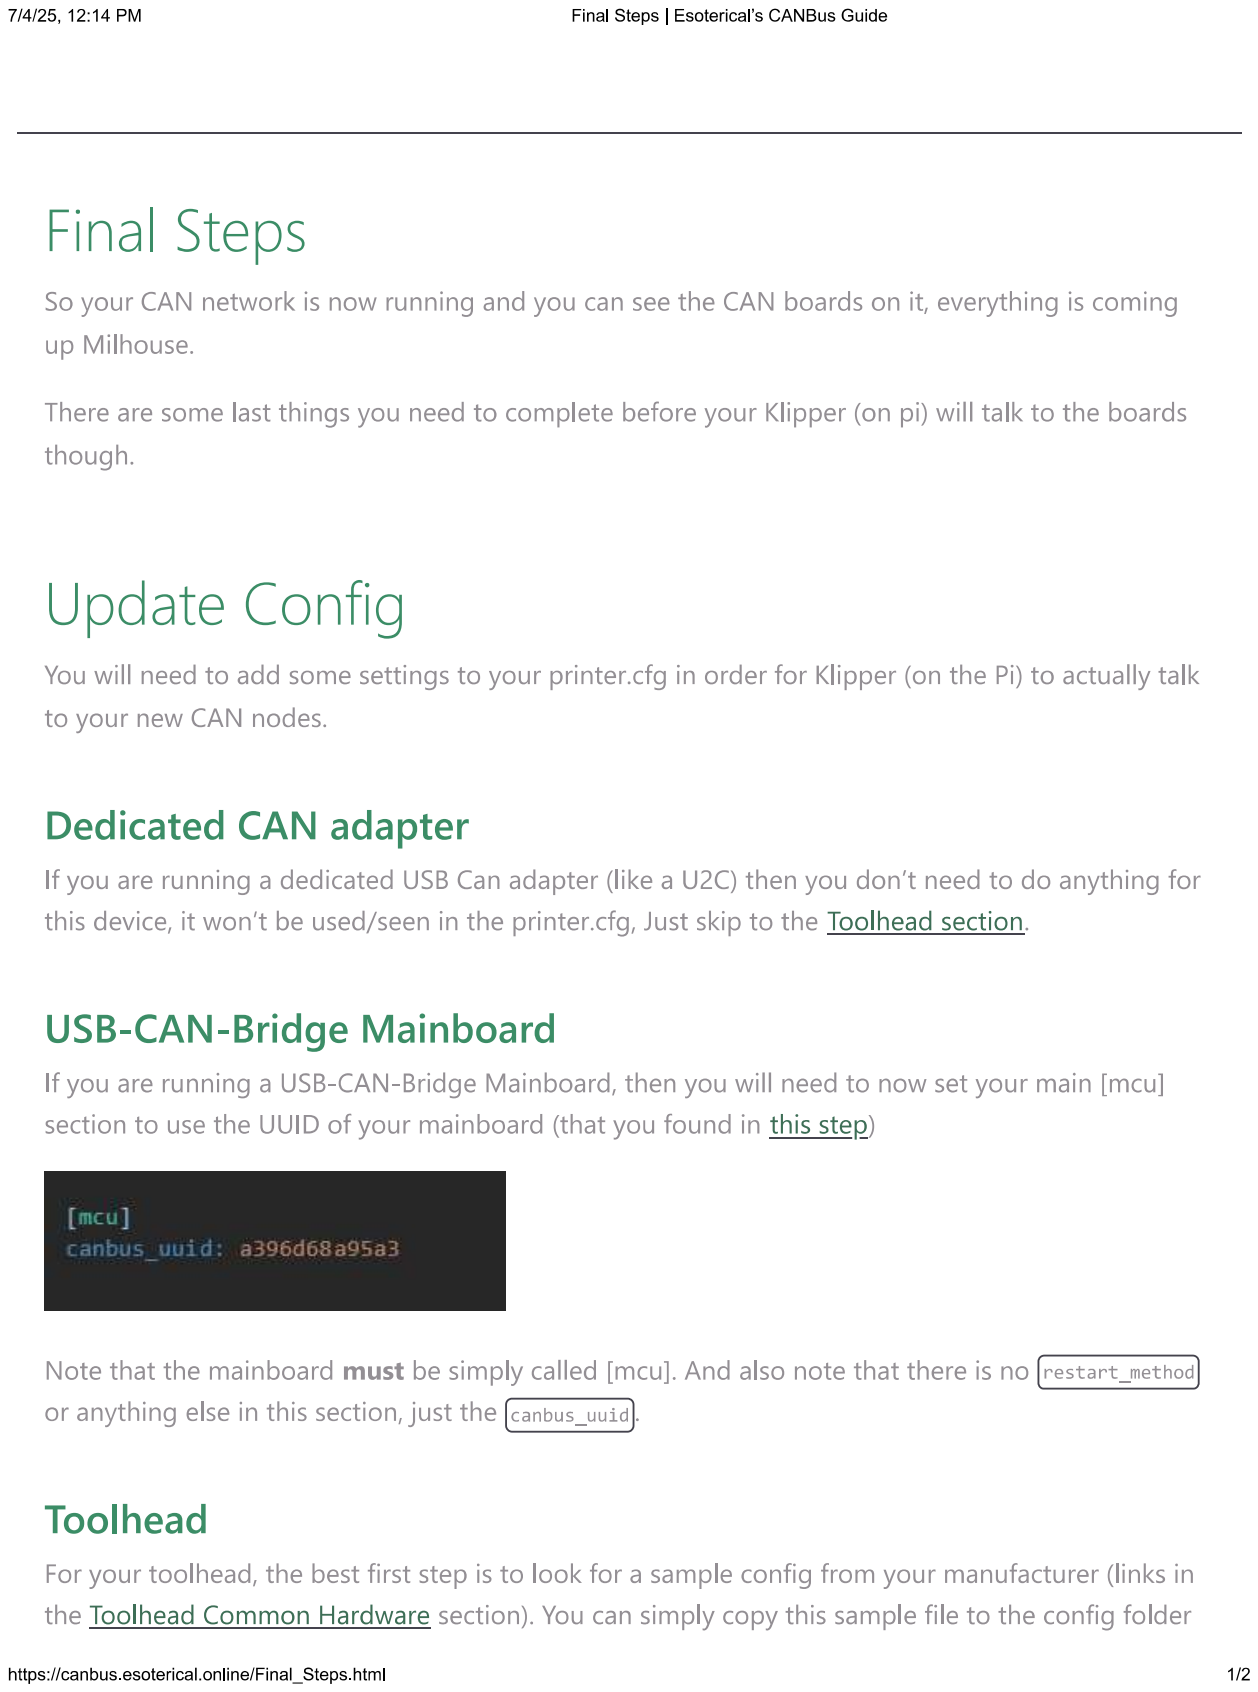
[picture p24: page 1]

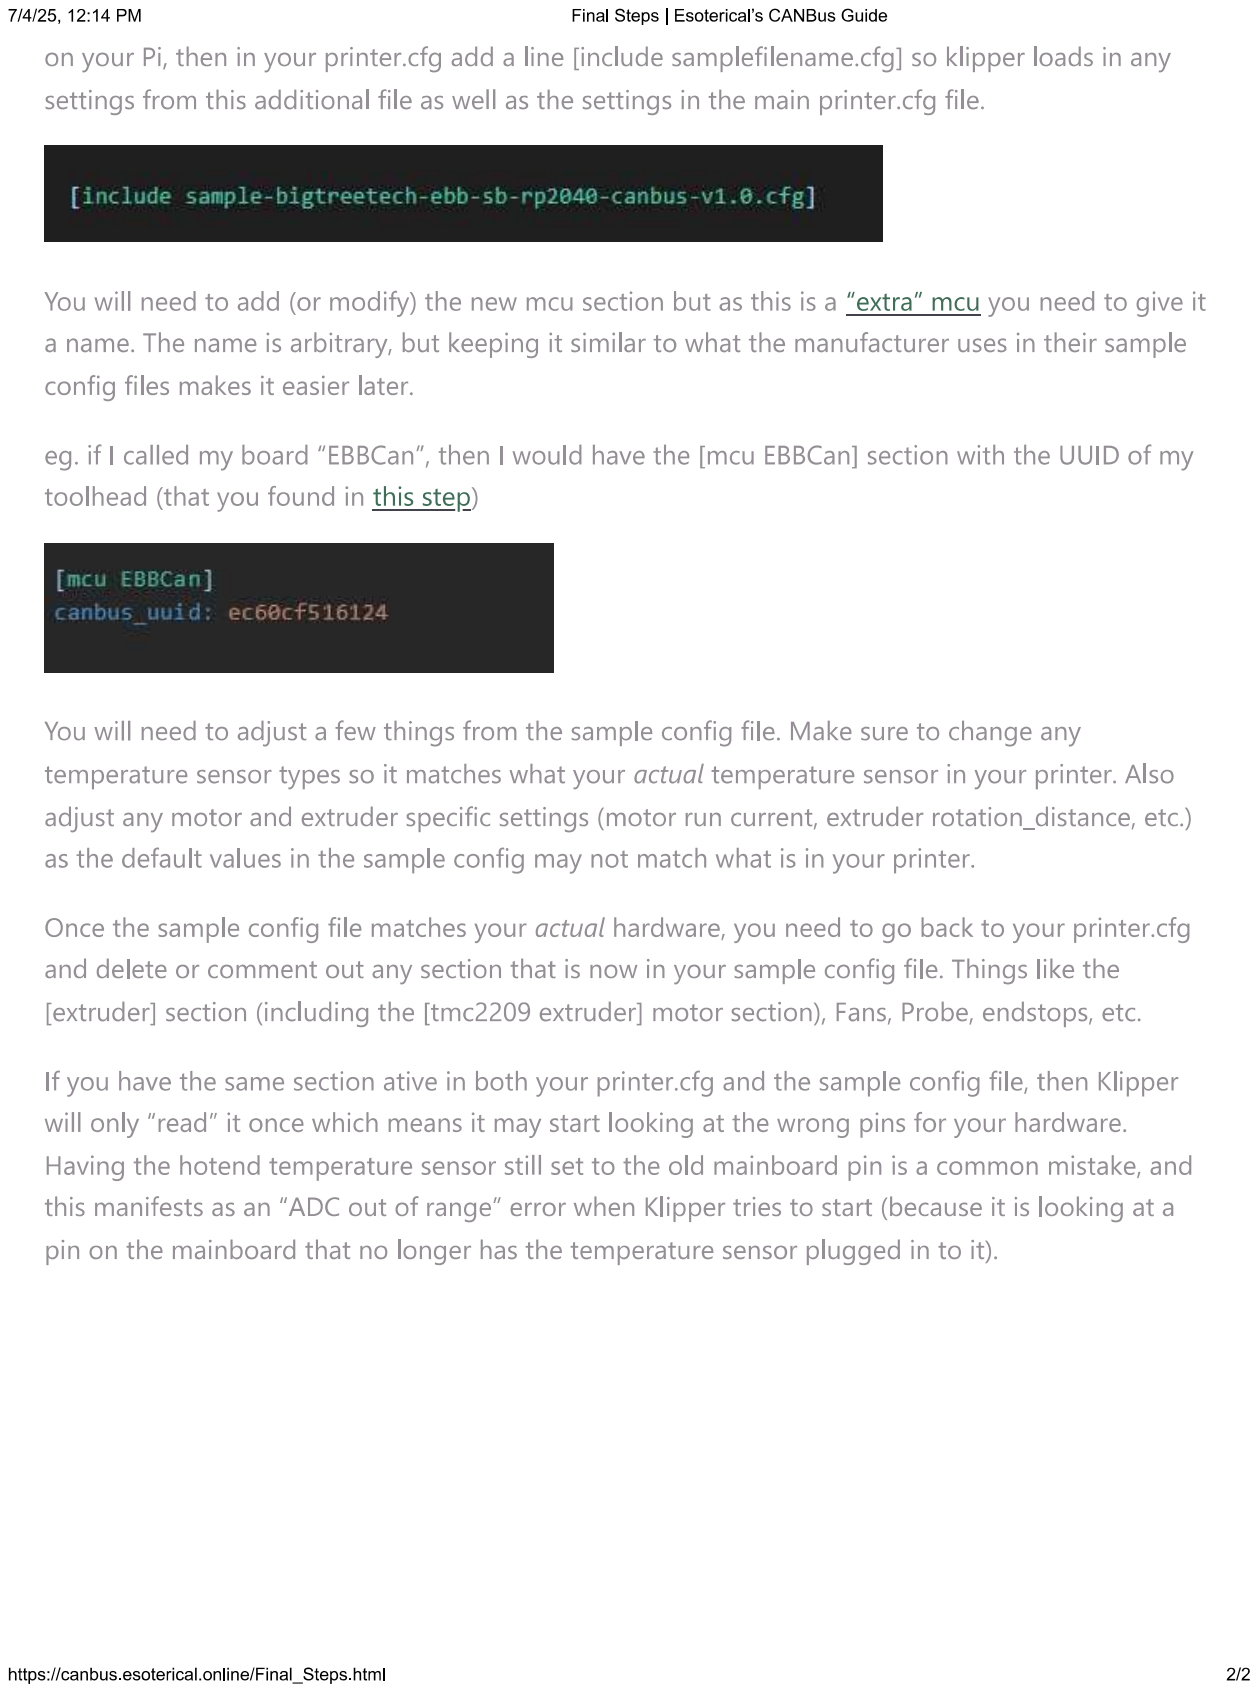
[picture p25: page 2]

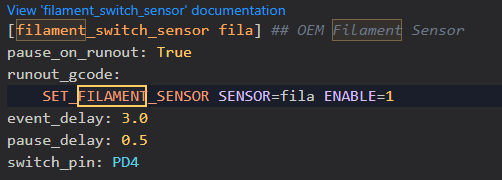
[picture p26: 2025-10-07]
BTT_smart_filament_detection_module_install_guide/Screenshot 2025-10-07 123641.png

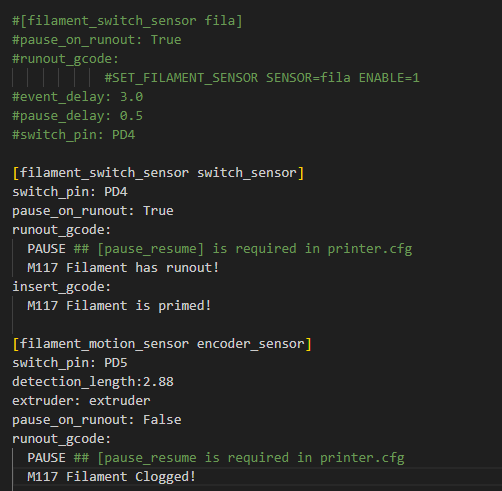
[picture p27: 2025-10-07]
BTT_smart_filament_detection_module_install_guide/Screenshot 2025-10-07 130252.png

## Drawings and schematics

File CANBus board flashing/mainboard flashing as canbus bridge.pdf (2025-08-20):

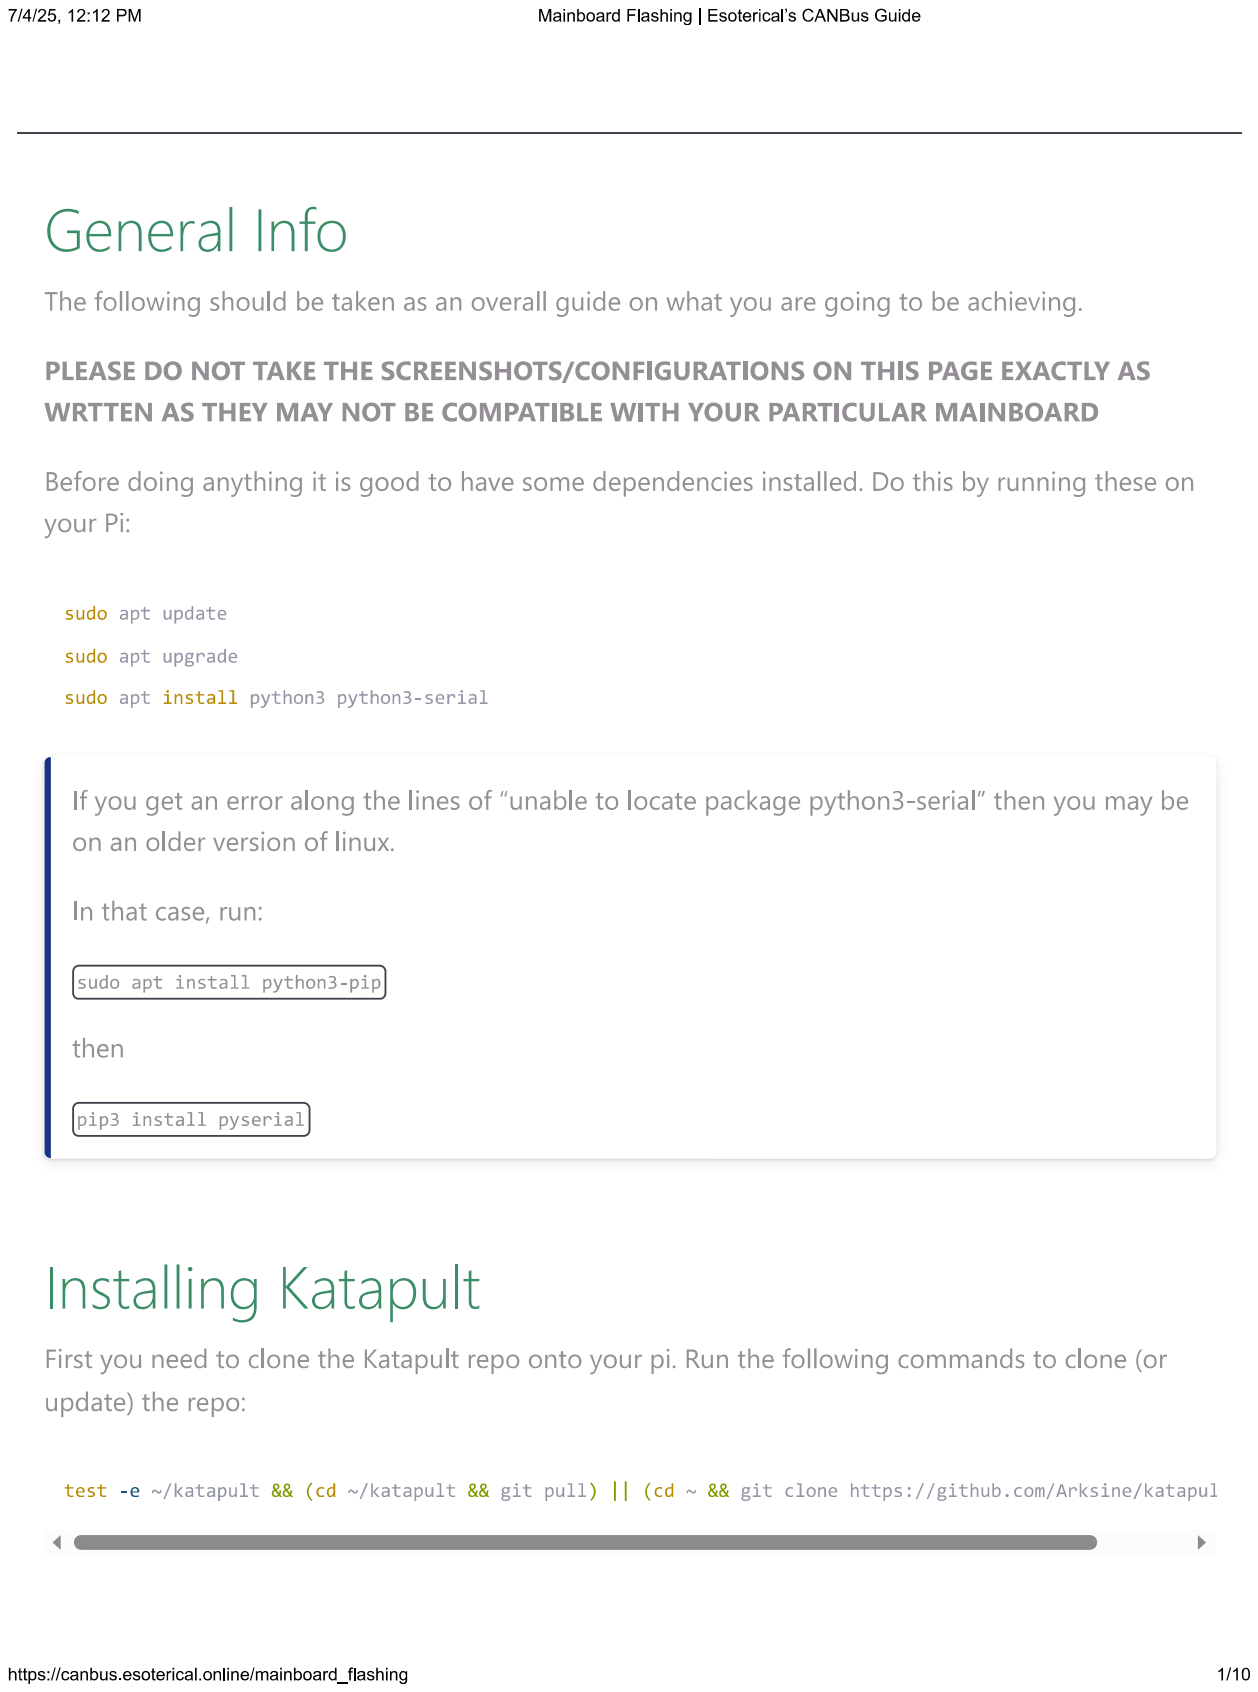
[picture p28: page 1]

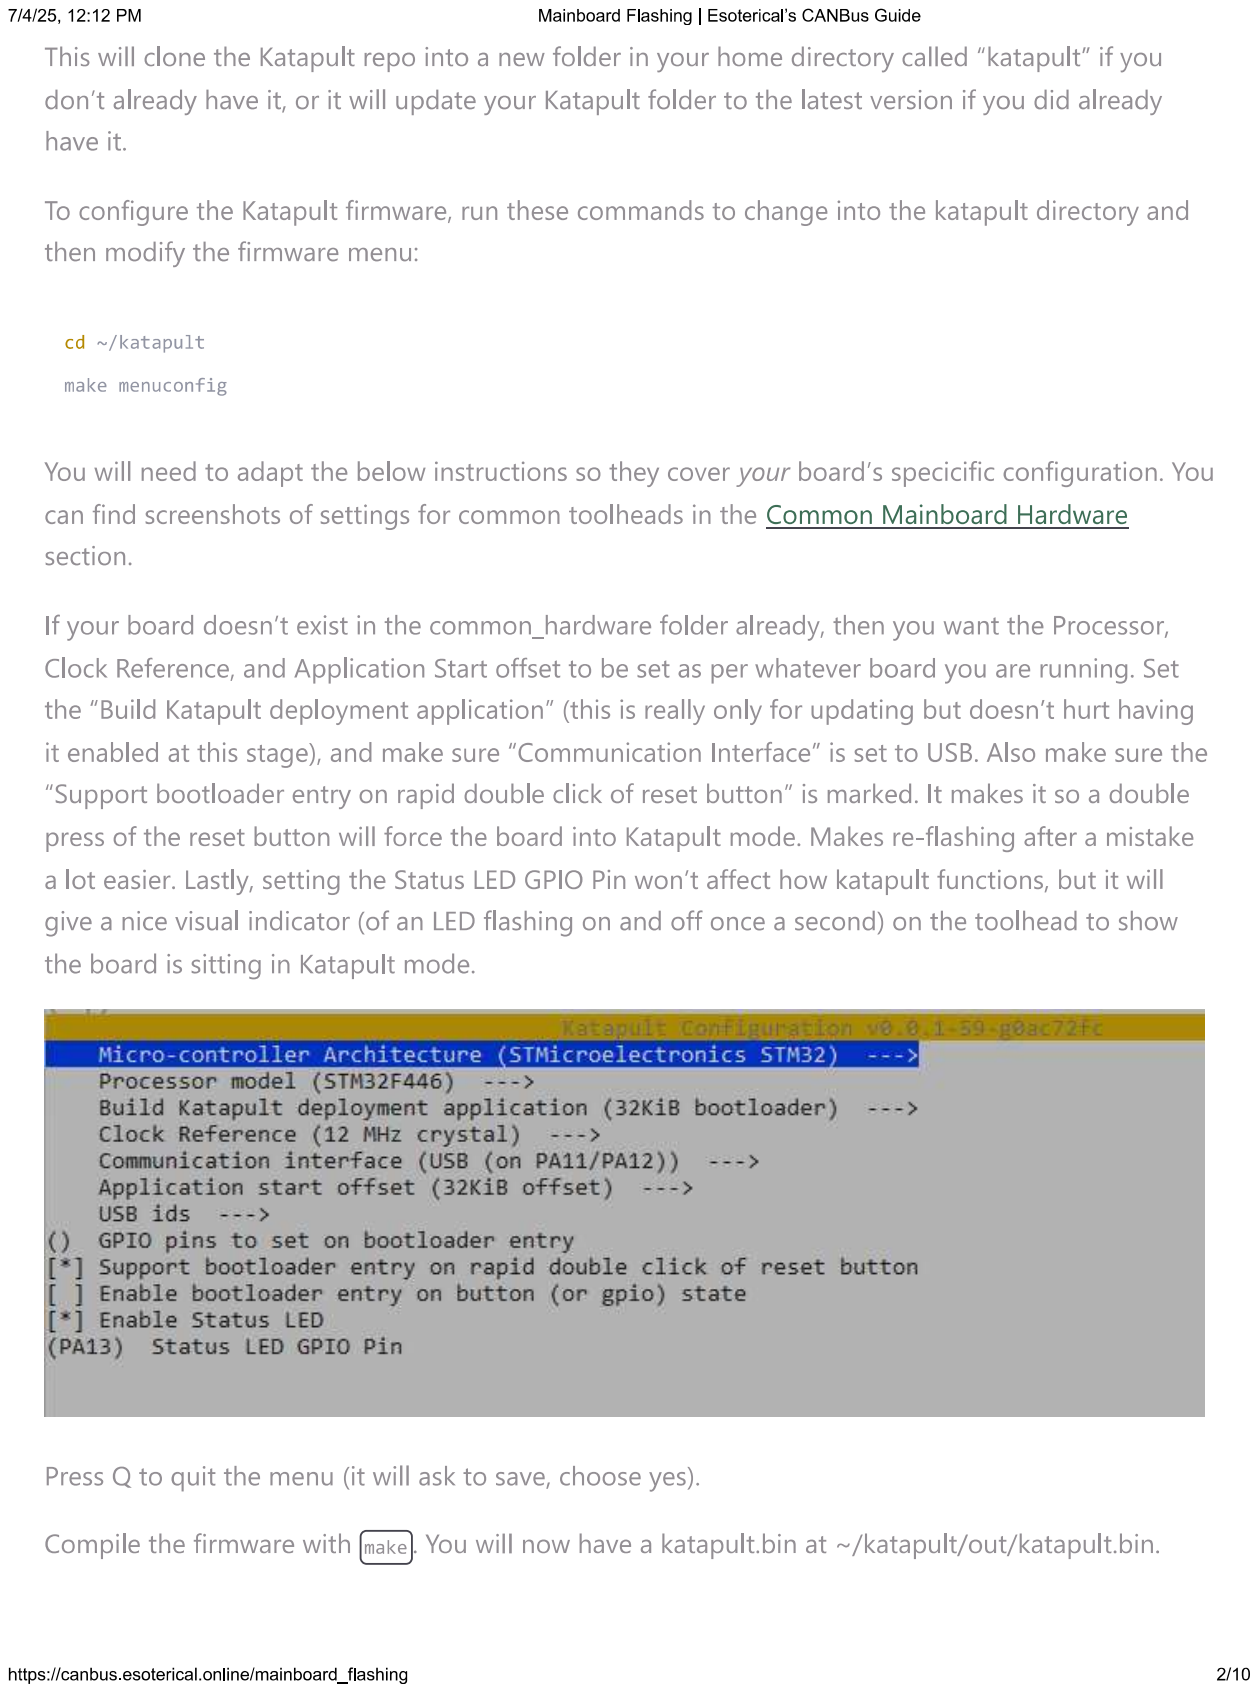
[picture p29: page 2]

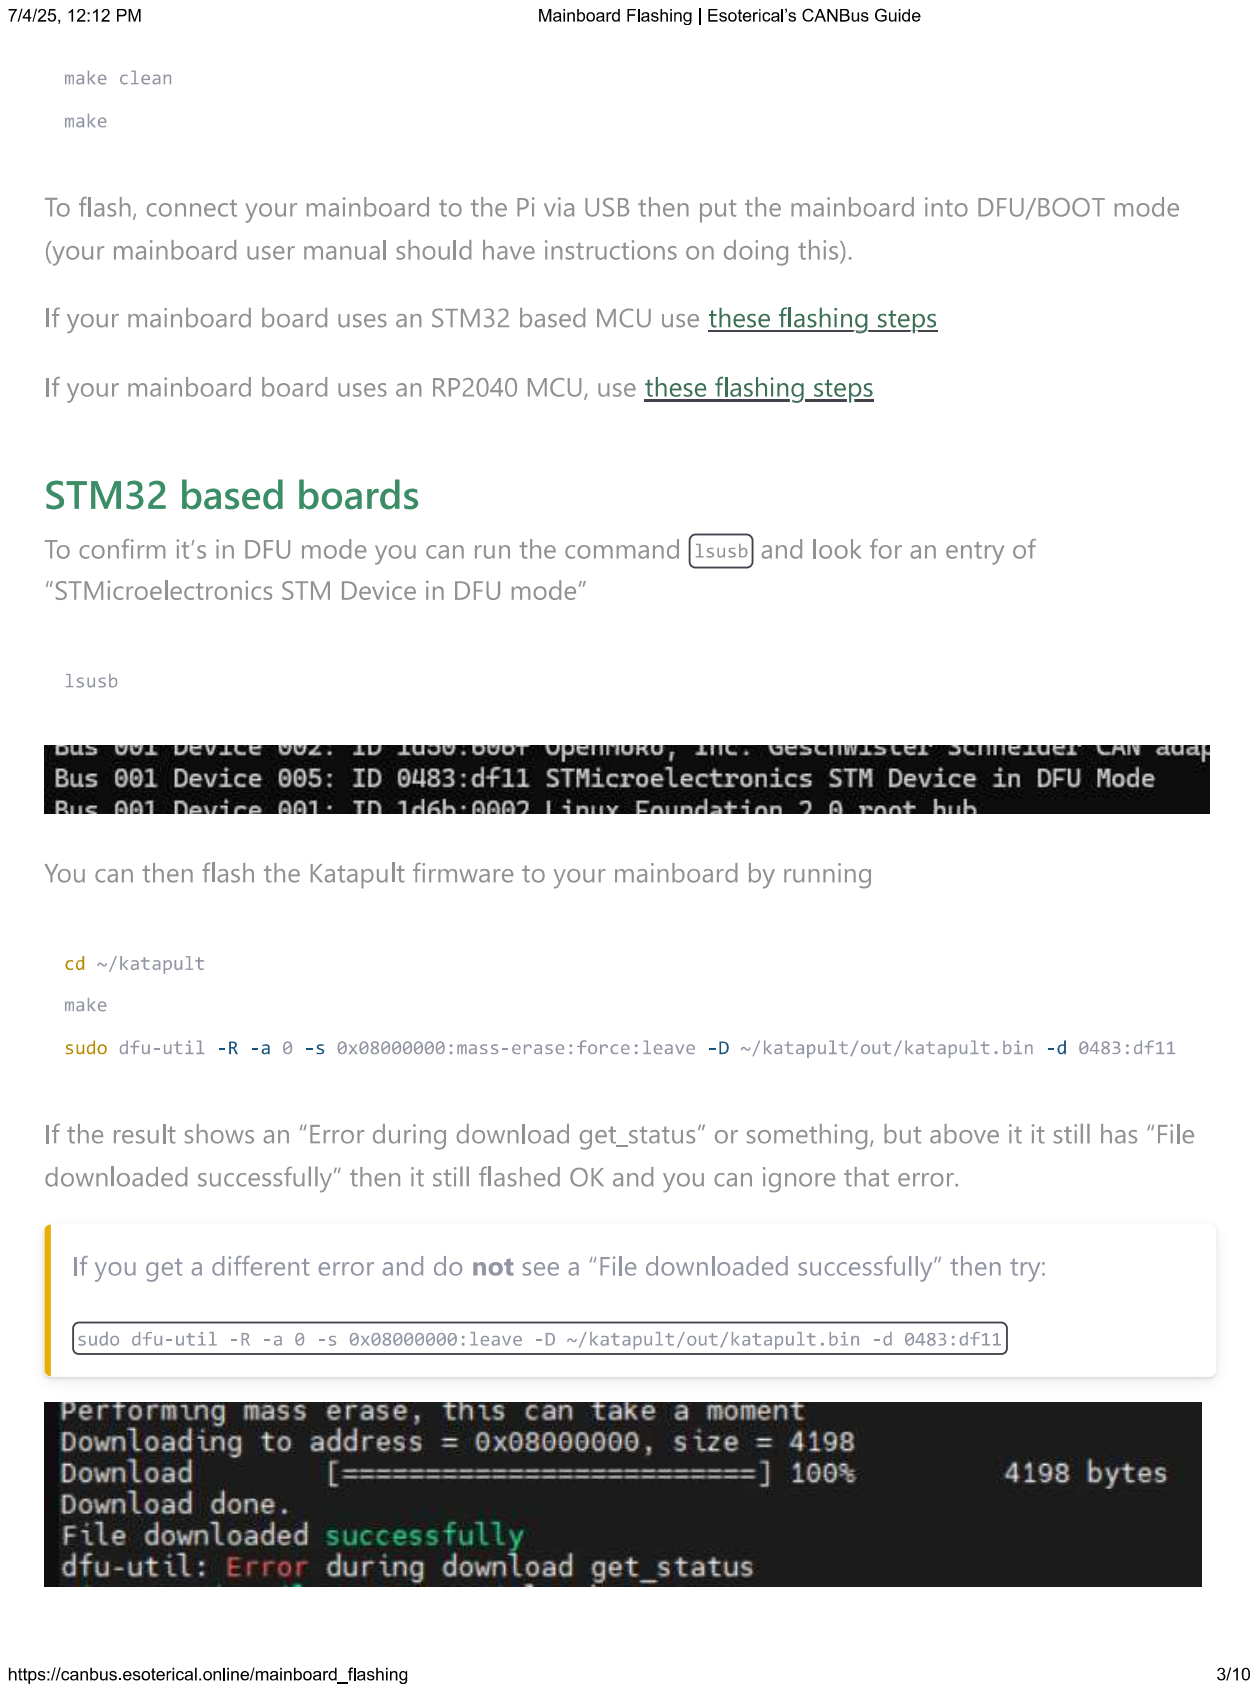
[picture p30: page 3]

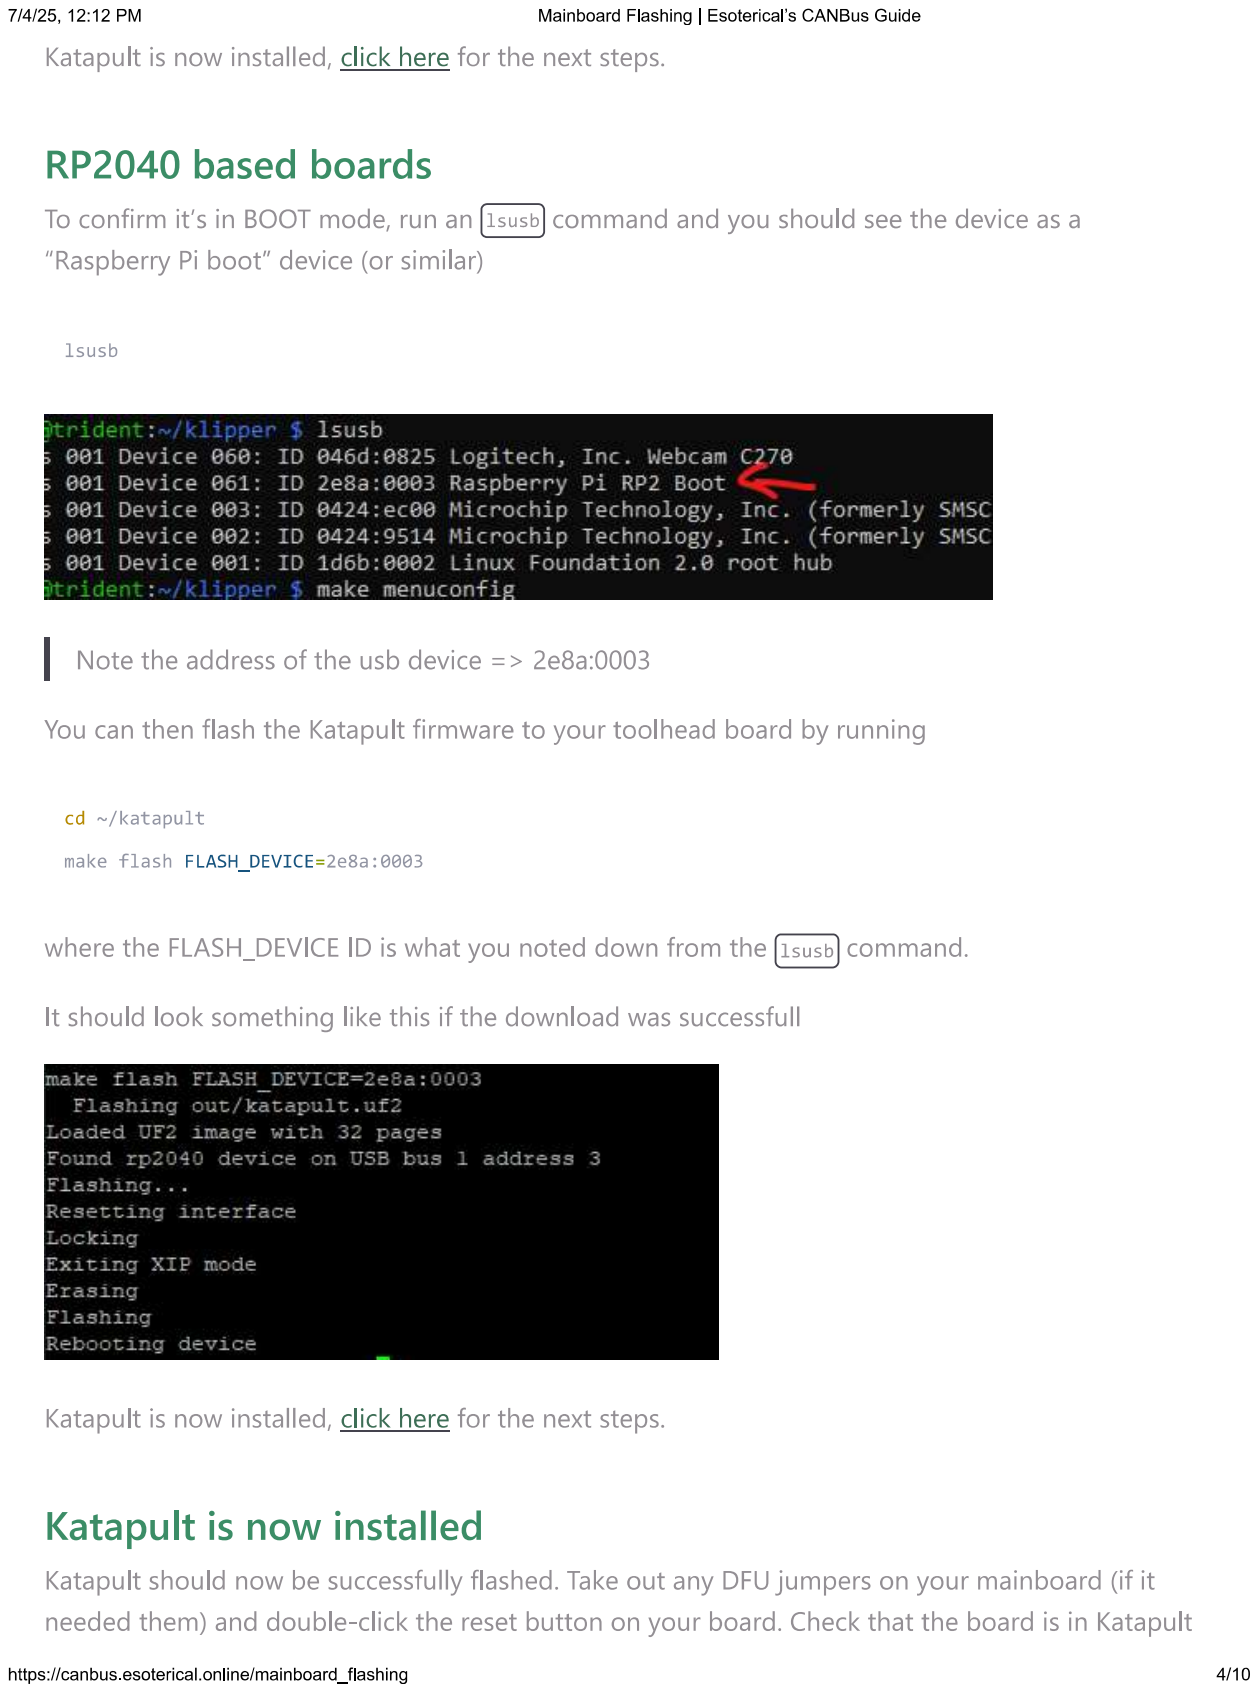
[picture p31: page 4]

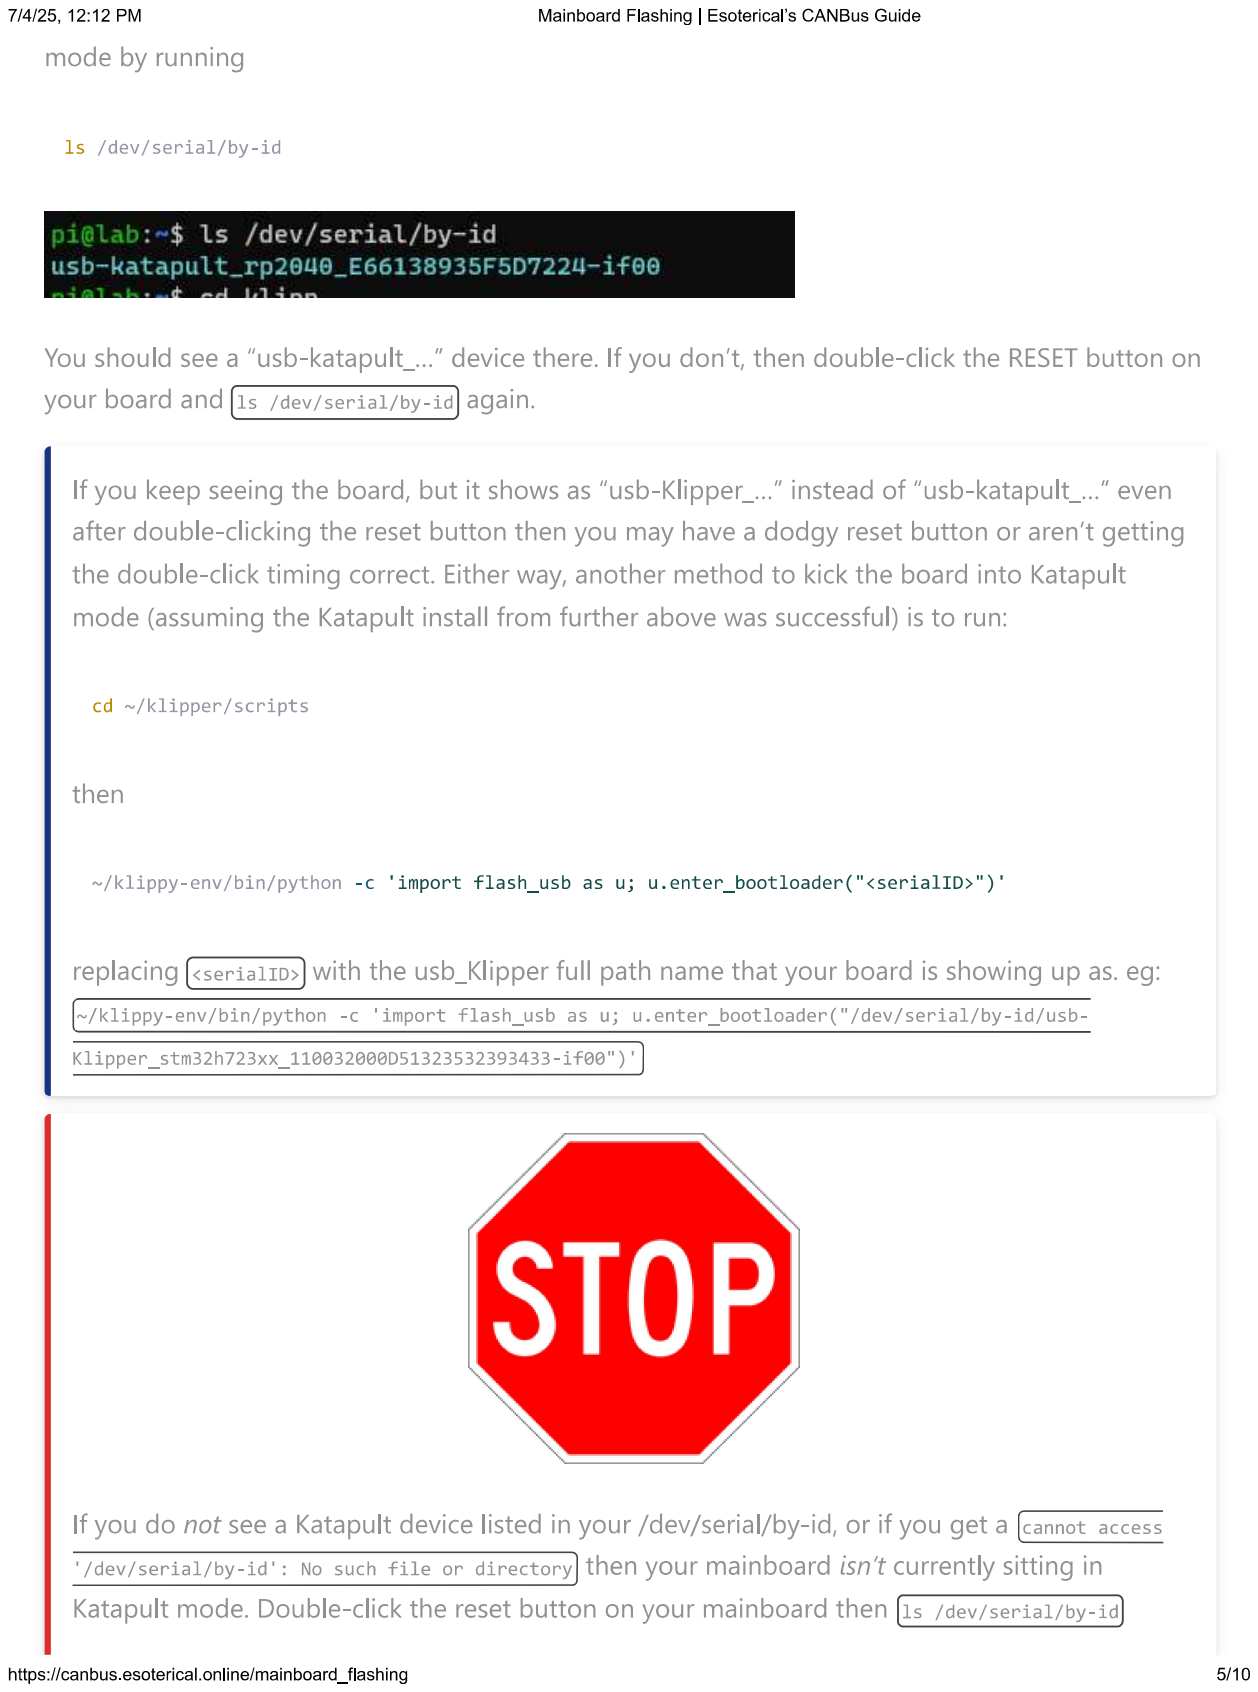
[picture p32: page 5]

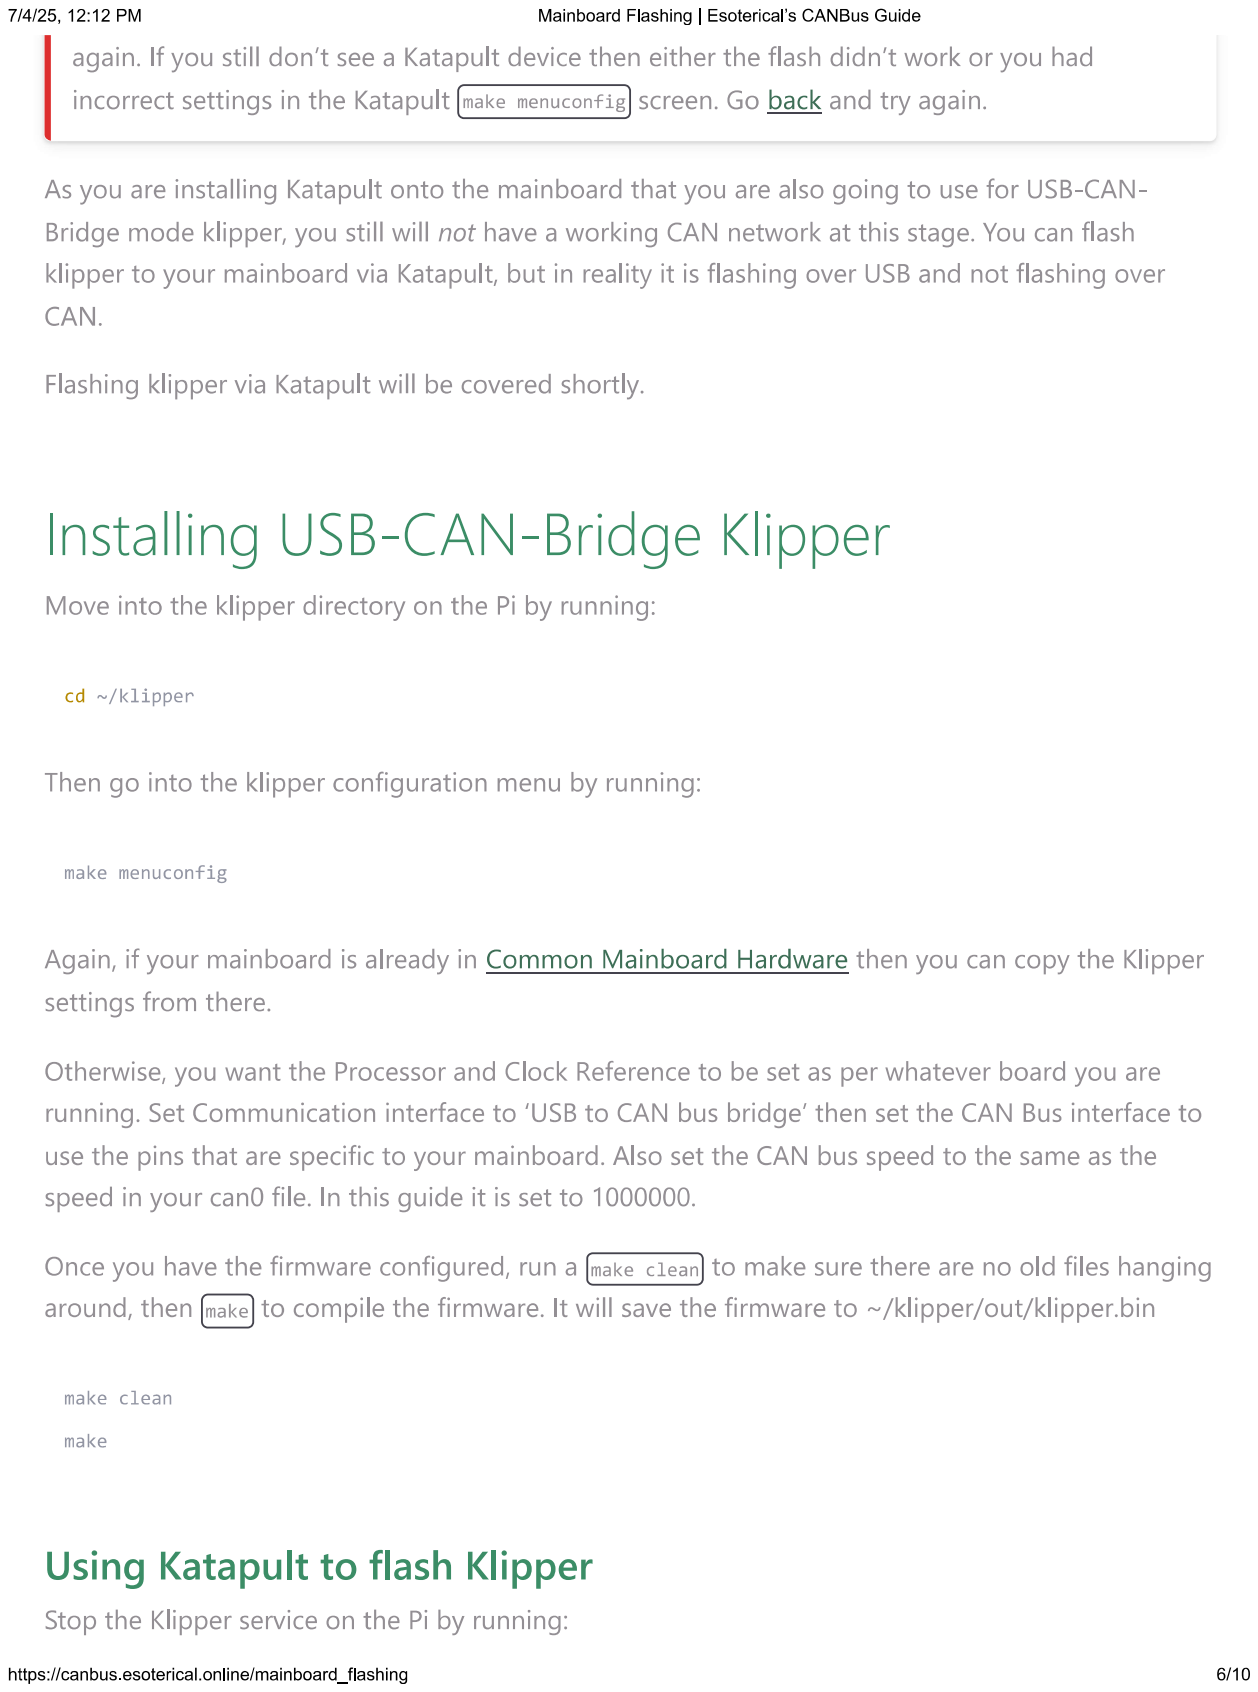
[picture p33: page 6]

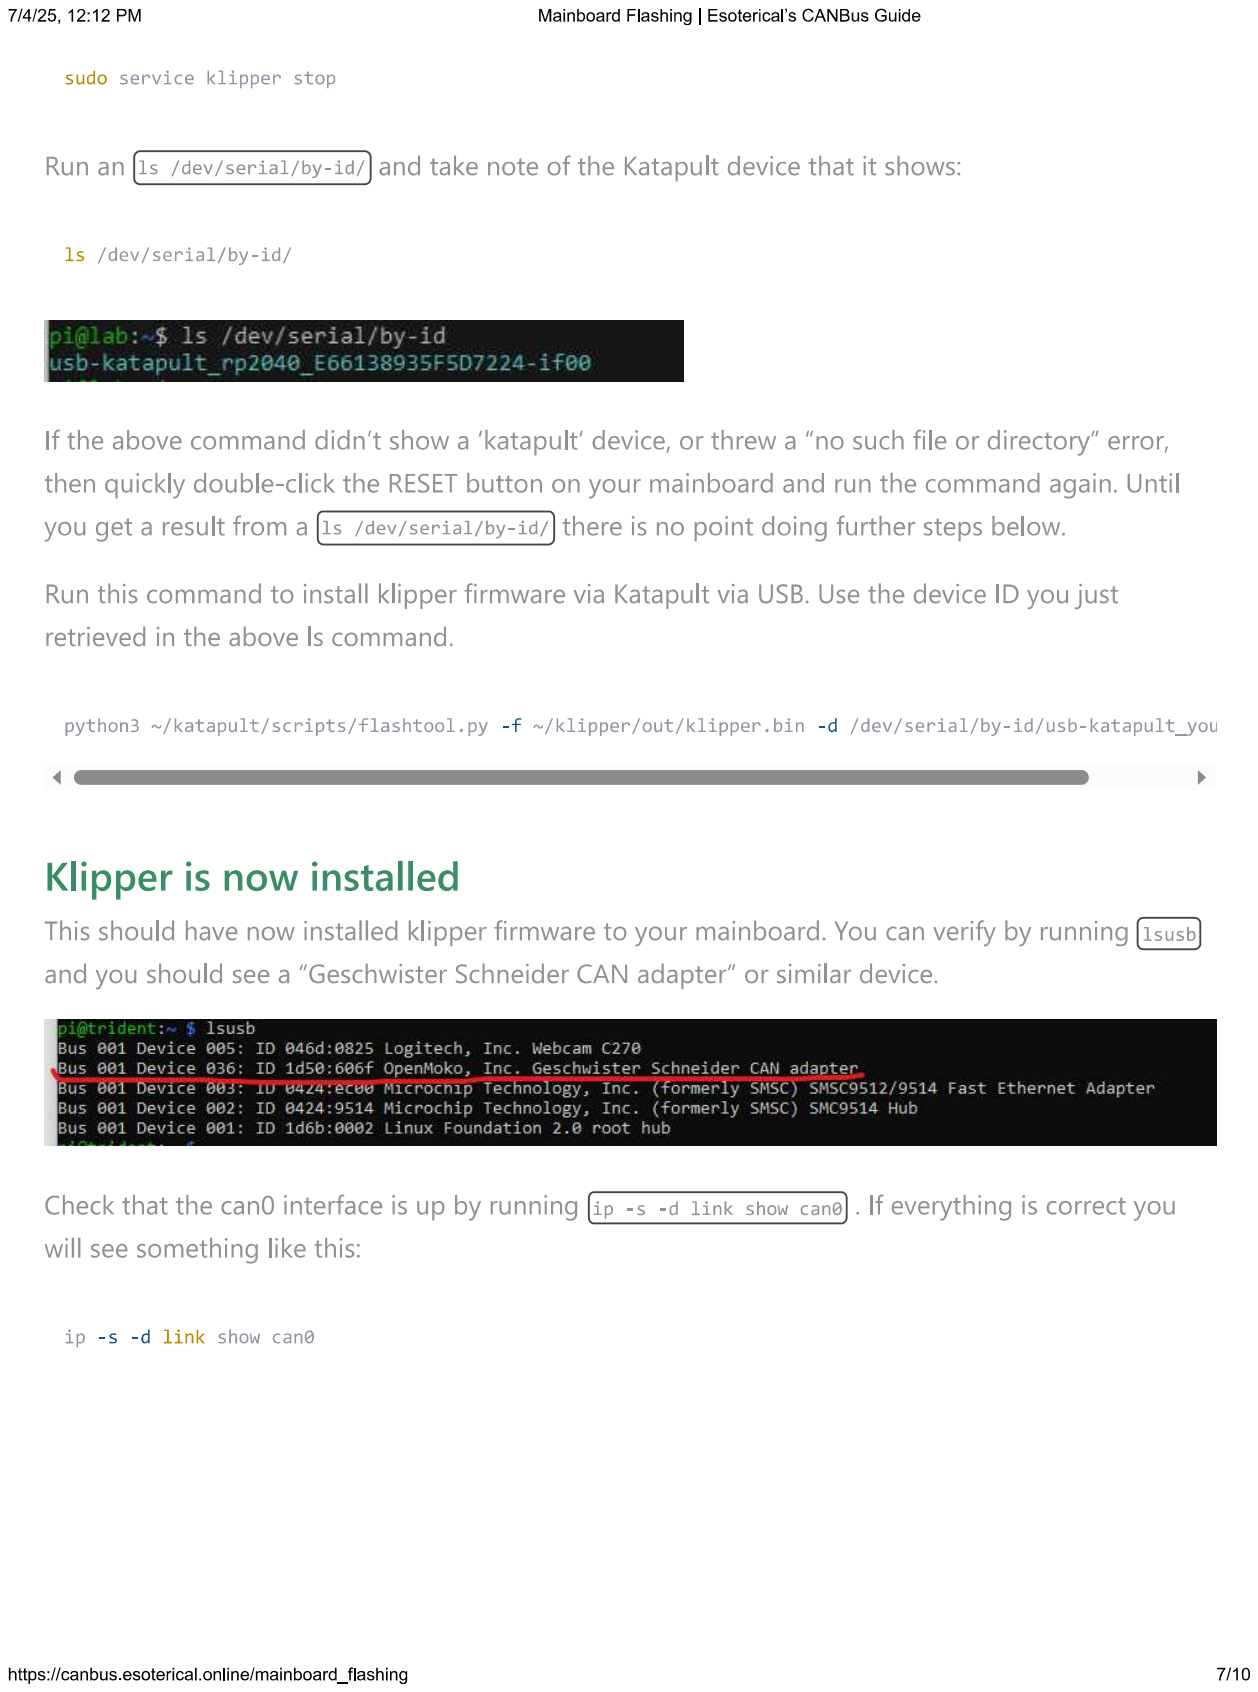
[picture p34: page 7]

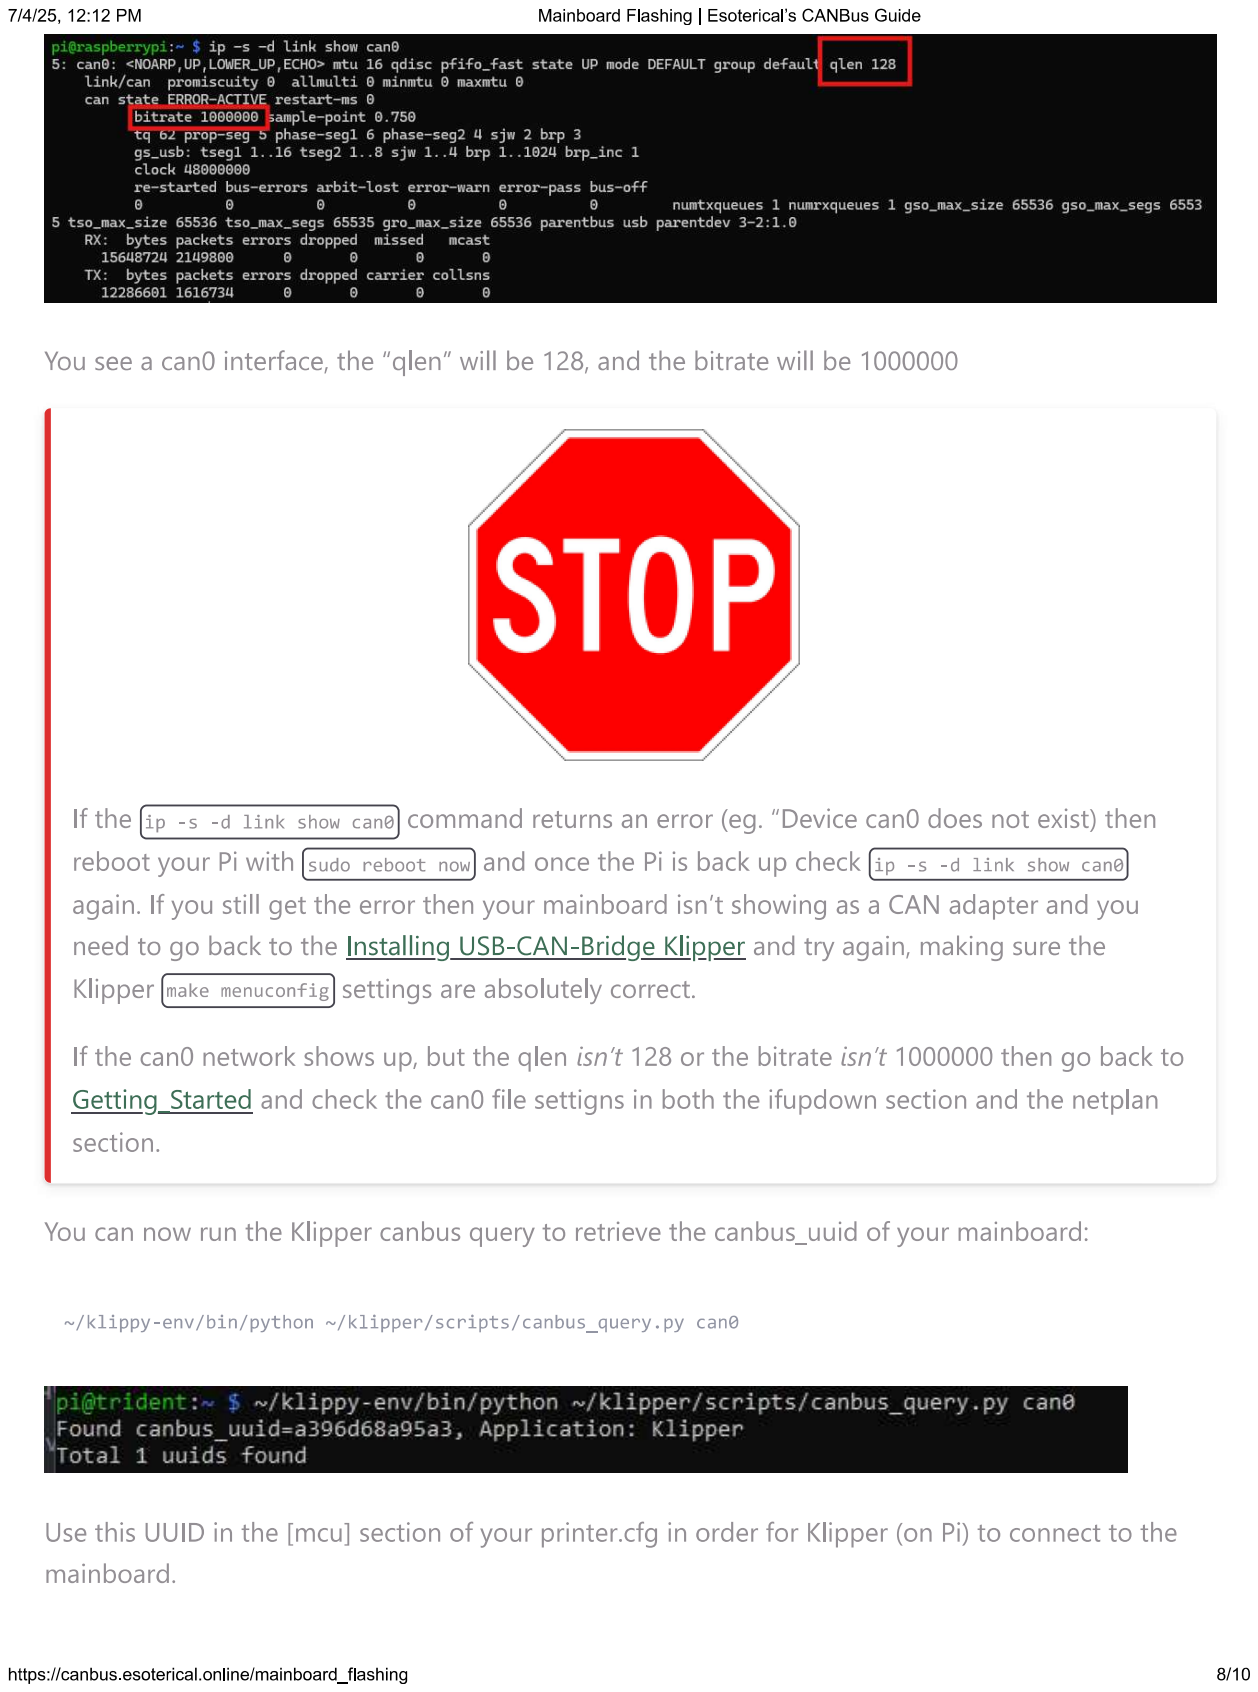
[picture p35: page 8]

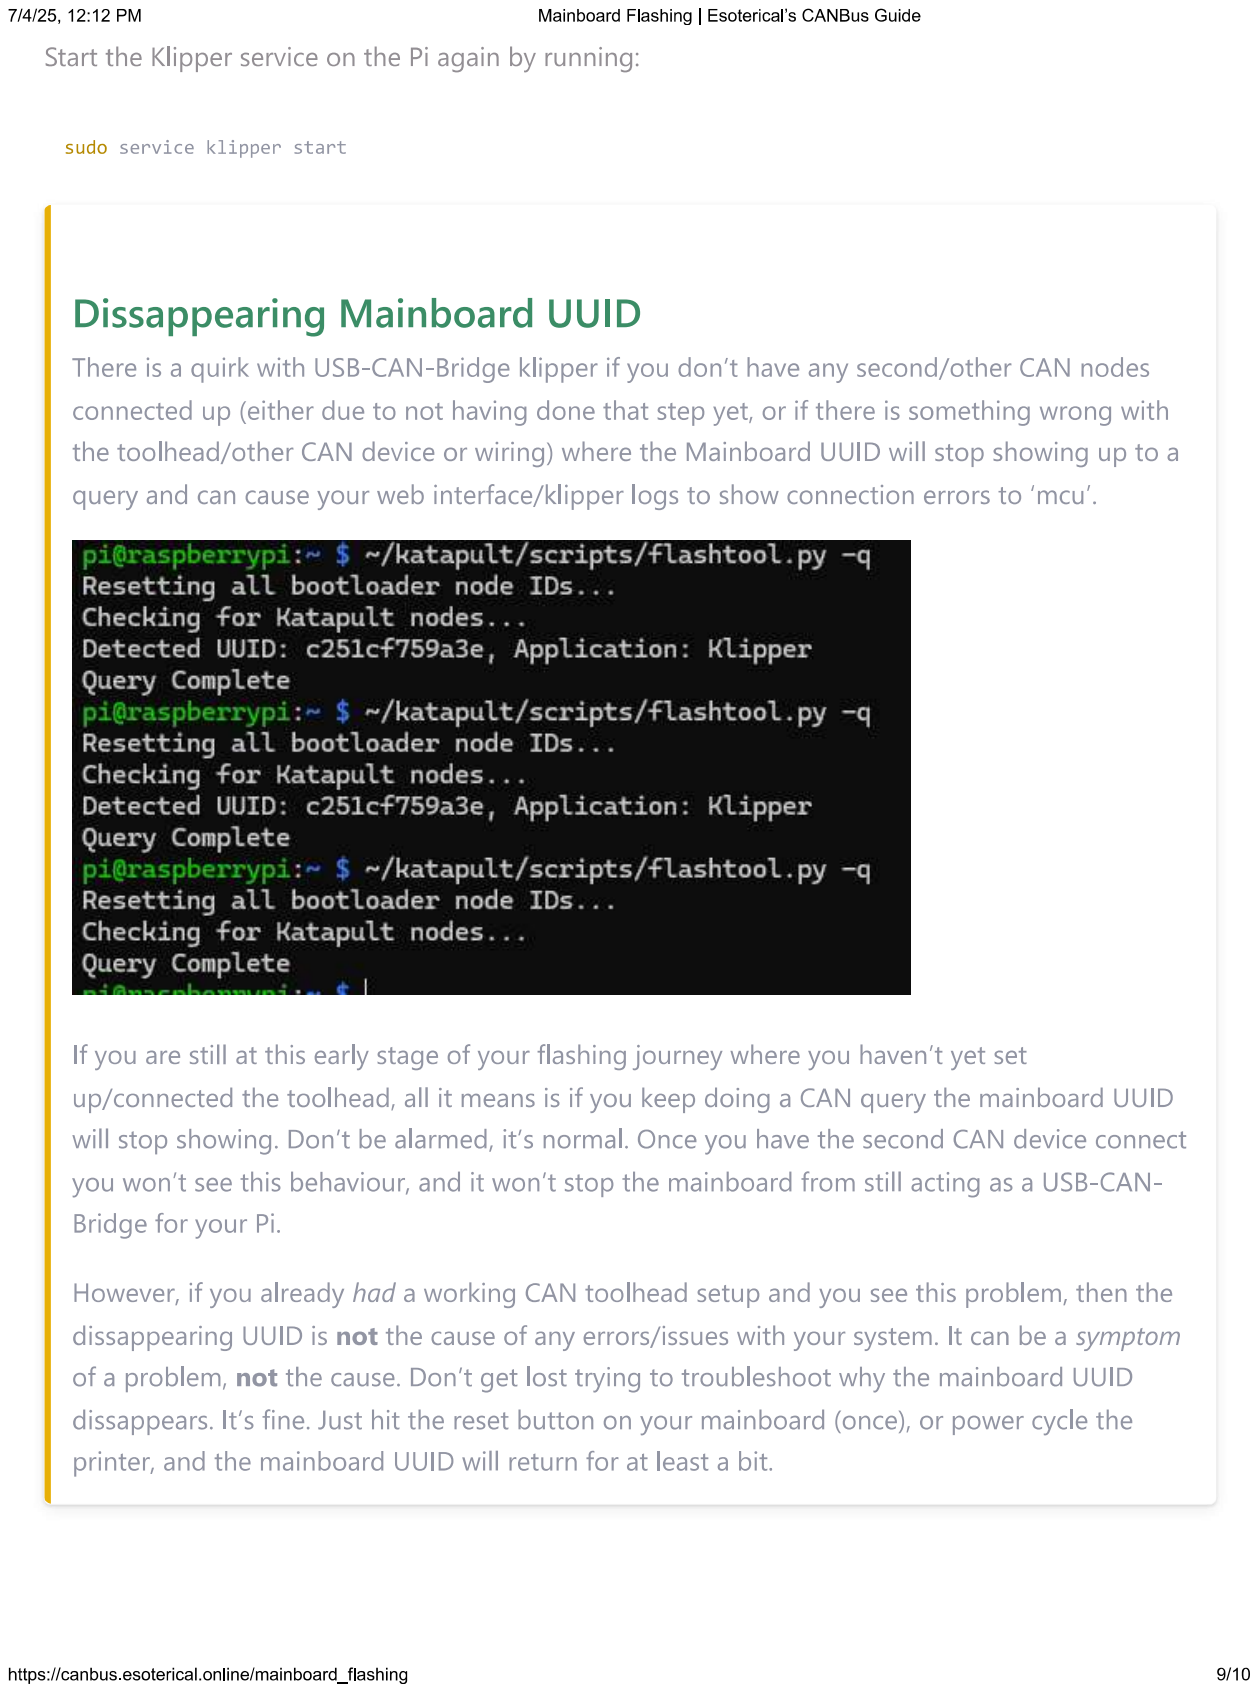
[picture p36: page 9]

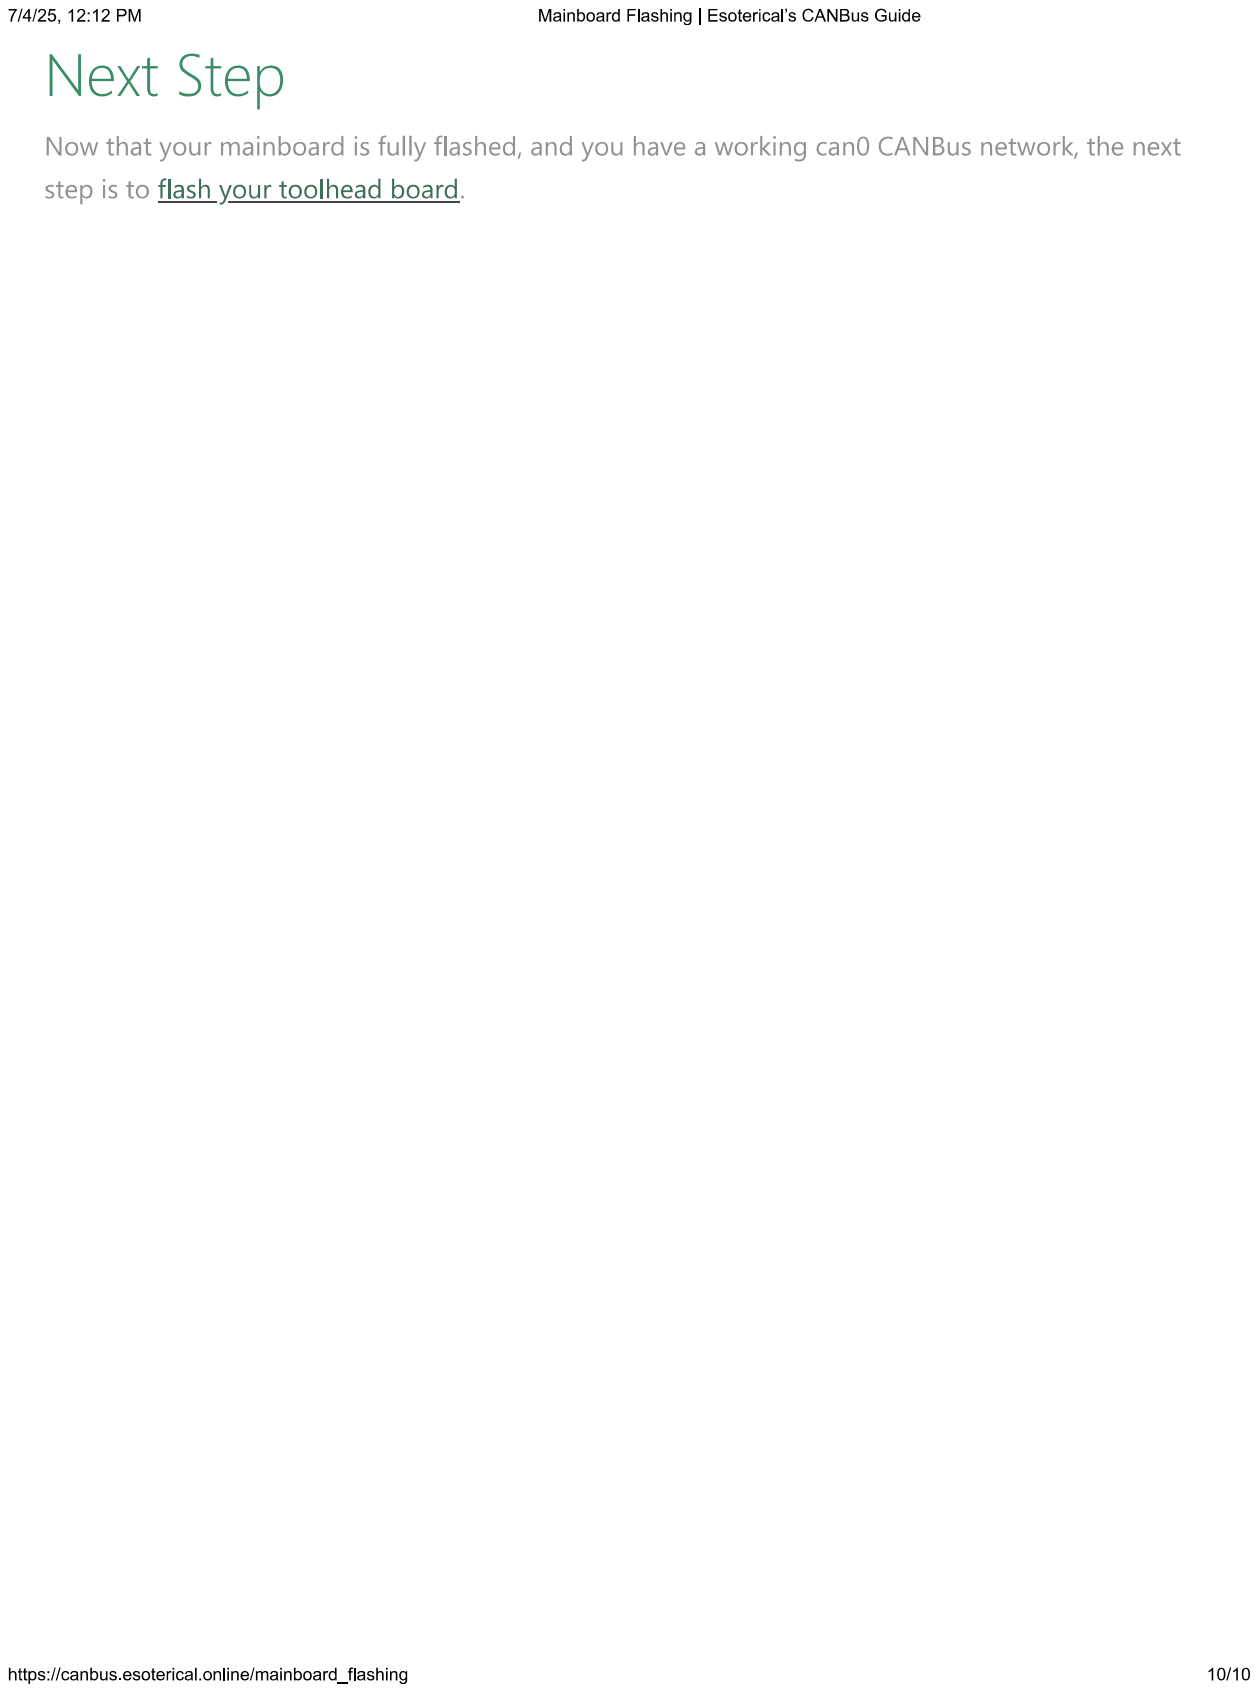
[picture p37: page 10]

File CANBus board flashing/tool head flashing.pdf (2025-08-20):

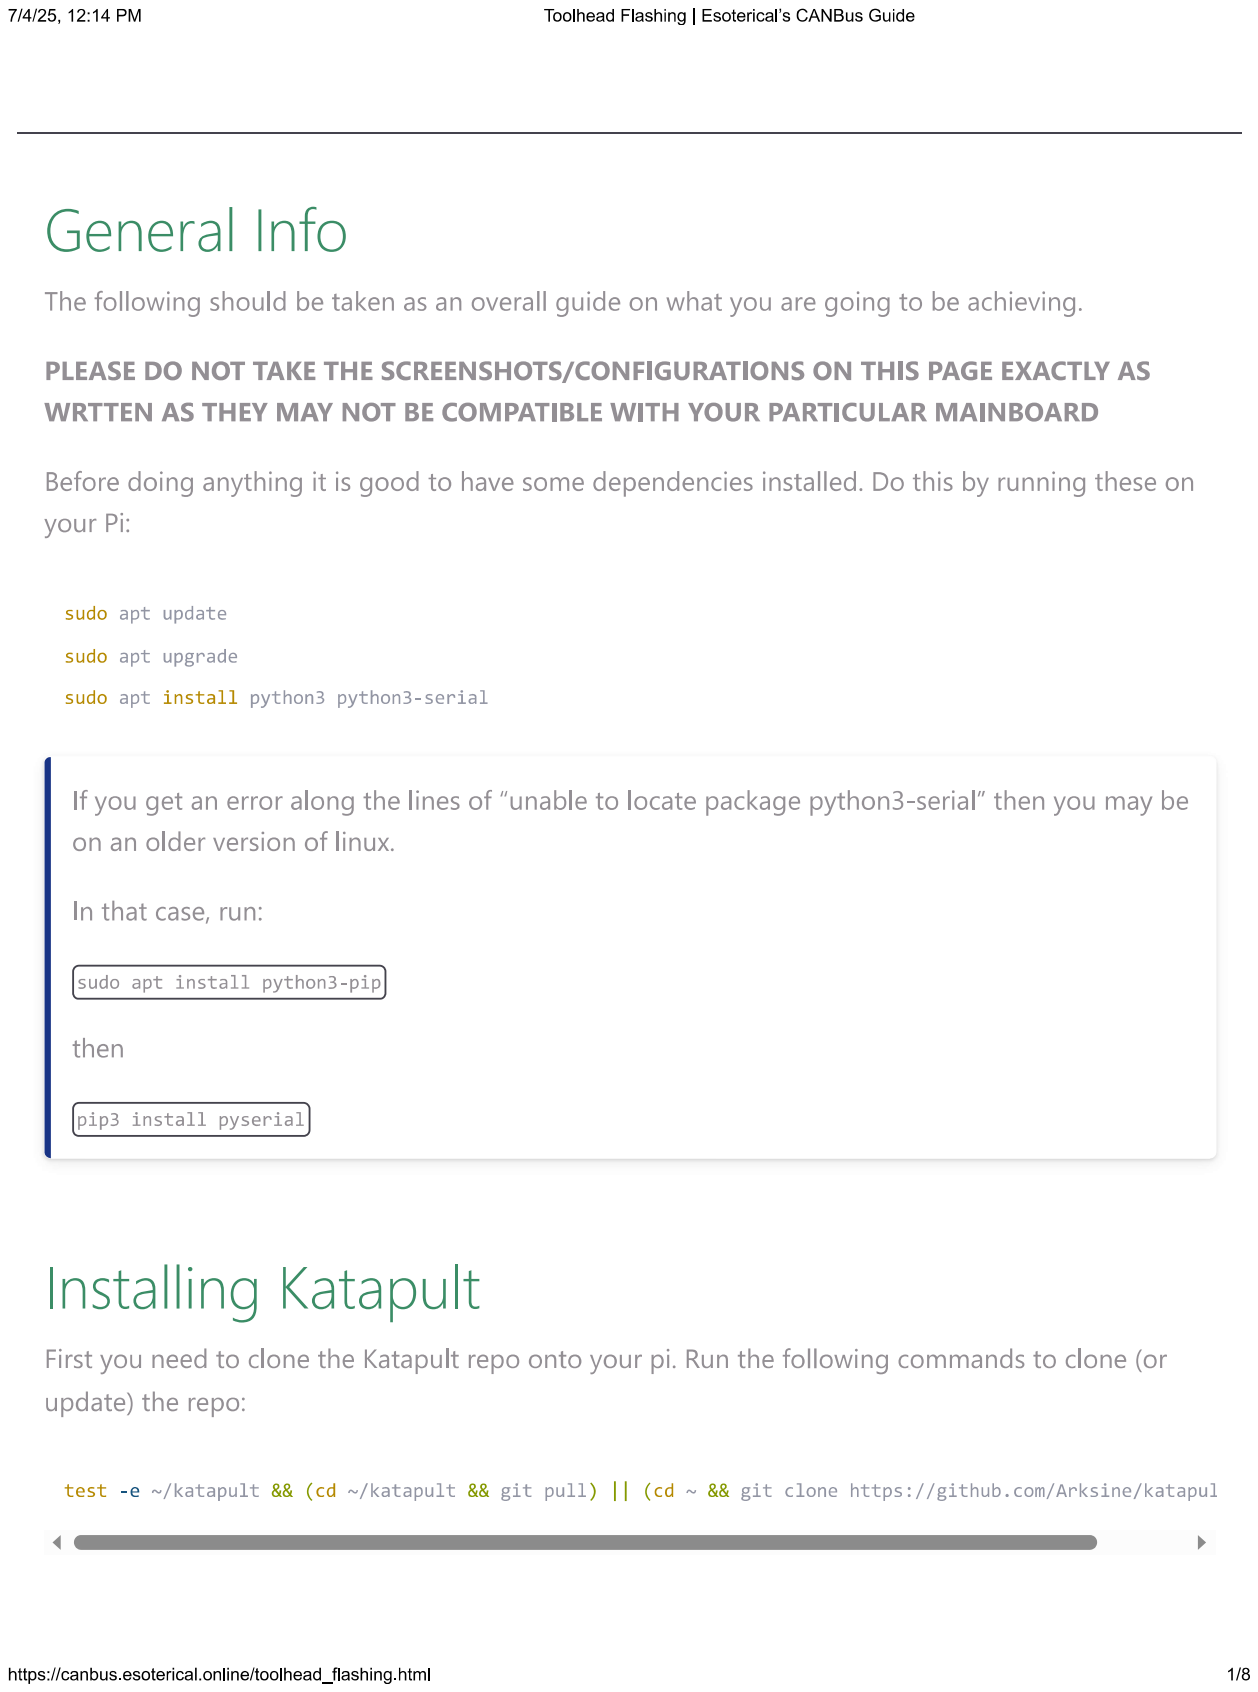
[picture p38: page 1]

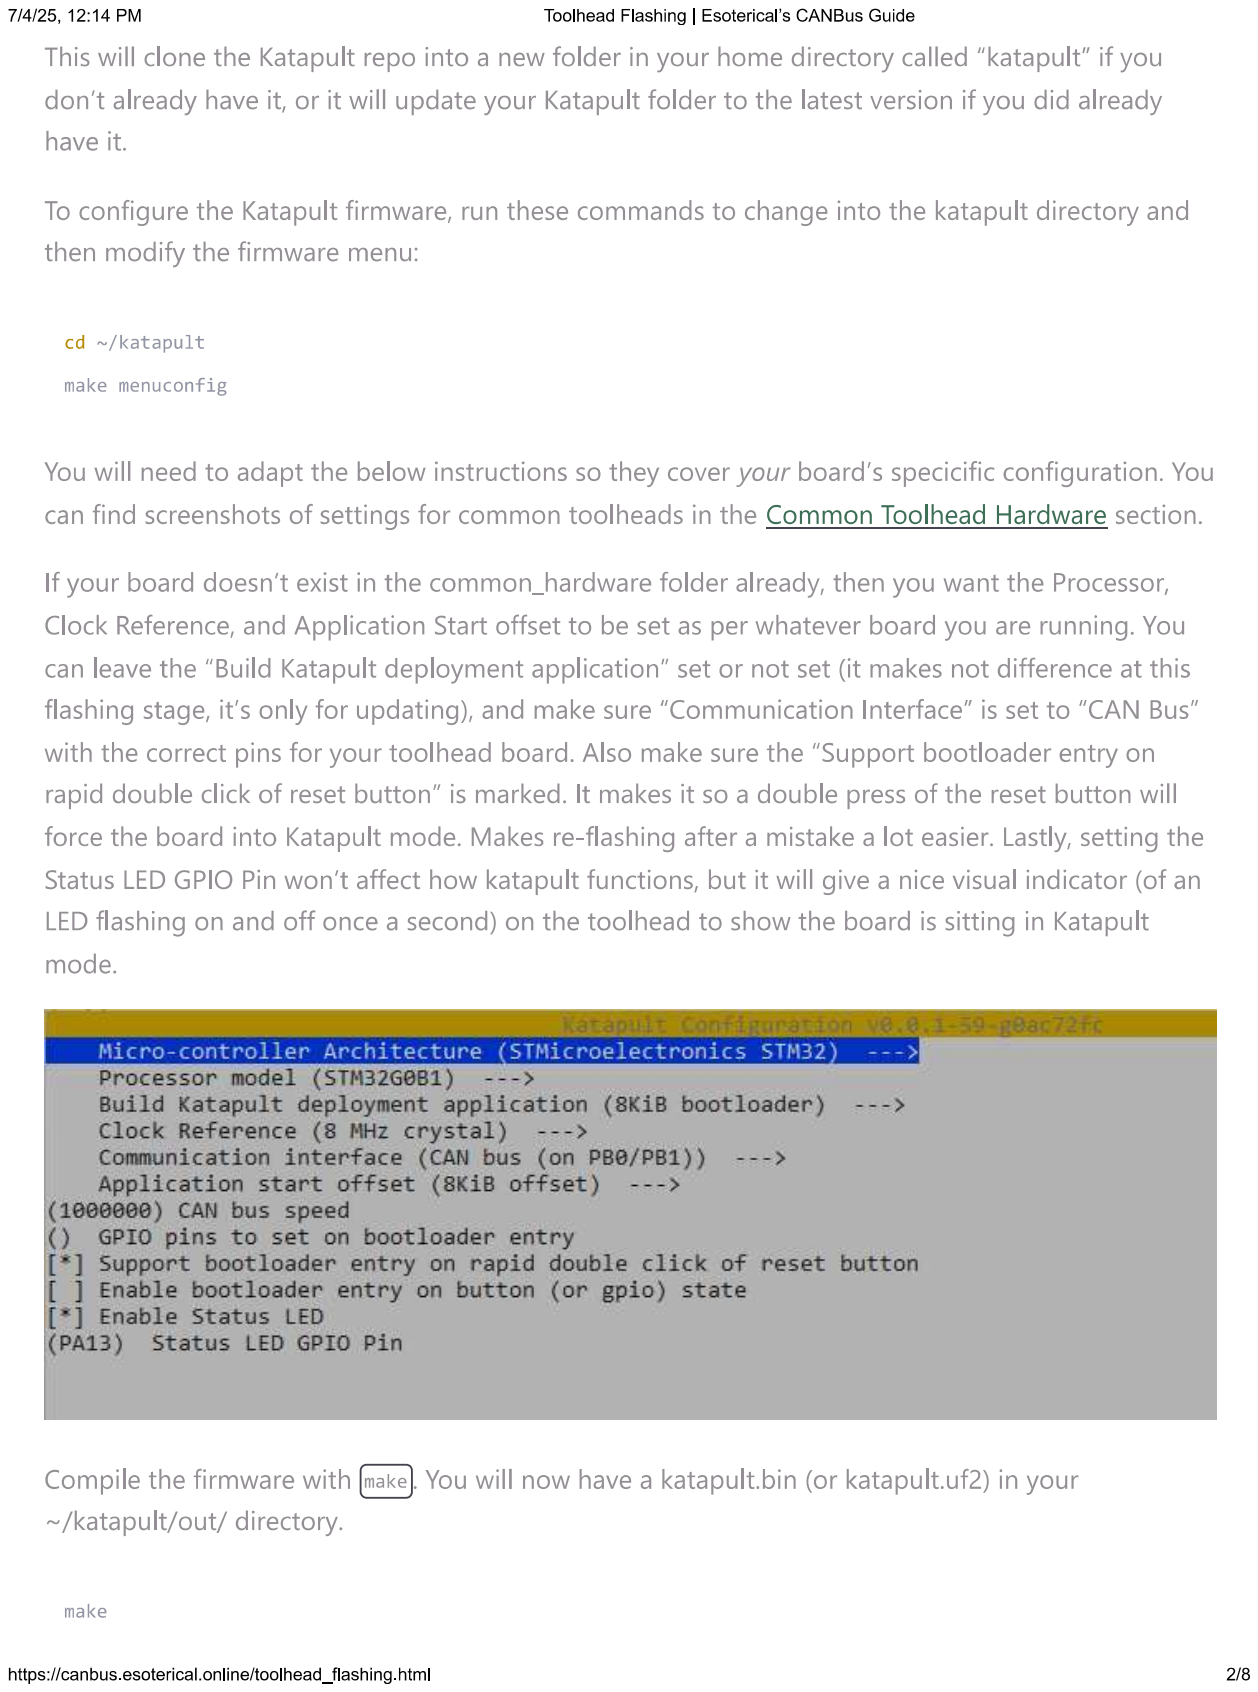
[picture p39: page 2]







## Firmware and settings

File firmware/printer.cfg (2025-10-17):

####################################################################################
# Machine type: JcwGiga
# Current configuration version: VBeta
# Date：2025-10-01
####################################################################################

[mcu]
canbus_uuid: xxxxxxxxxxxxx #Put your mainboard CANBus ID here
canbus_interface: can0

[include plr.cfg]
[include fluidd.cfg]
#[include EBBCanRP2040.cfg]		#EBB SB2209 (Raspberry pi chip)
#[include EBBCan.cfg]	#EBB SB2209 (STM chip)
#[include KAMP_Settings.cfg]
#[include timelapse.cfg]
[include Knomi.cfg]

[virtual_sdcard]
path: /home/biqu/printer_data/gcodes
on_error_gcode: CANCEL_PRINT

[include shell_command.cfg]
[include moonraker_obico_macros.cfg]

[force_move]
enable_force_move : true

[pause_resume]

[gcode_button kill_switch]	#Orangestorm Giga Estop at the front of the machine
pin: !PE11
press_gcode: M112

[display_status]
[gcode_arcs]
[exclude_object]
[respond]

[save_variables]
filename: ~/printer_data/config/variables.cfg

[auto_speed]

[idle_timeout]
timeout: 7200
gcode:
    {% if printer[printer.toolhead.extruder].temperature > 160 %}
    {action_respond_info("Extruder powered down on idle timeout.")}
    SET_HEATER_TEMPERATURE HEATER=extruder TARGET={140}
    SET_IDLE_TIMEOUT TIMEOUT=259200
    {% else %}
    TURN_OFF_HEATERS
    {% endif %}
    
[printer]
kinematics:cartesian
max_velocity: 500	#modified x and y axis, OEM Giga Value is 500
max_accel: 15000	#modified x and y axis, OEM Giga value is 5000
#max_accel_to_decel: 5000	#Klipper version 12 required this but 13 does not
max_z_velocity: 20
max_z_accel: 300	#modified z axis, OEM Giga Value is 200
square_corner_velocity: 5.0

###############################################################
## X/Y Stepper Settings
###############################################################

[stepper_x]
step_pin: PF13
dir_pin: !PF12
enable_pin: !PF14
microsteps: 16
rotation_distance: 59.8519
full_steps_per_rotation:200  #set to 400 for 0.9 degree stepper
endstop_pin: PG6
position_min: -5
position_endstop: 815
position_max: 815.5
homing_speed: 100	#max 100 OEM Giga value is 80
homing_retract_dist:10
second_homing_speed:10
homing_positive_dir:true
step_pulse_duration:0.000002

[stepper_y]
step_pin:PG0
dir_pin:PG1
enable_pin:!PF15
microsteps:16
rotation_distance: 59.8519
full_steps_per_rotation:200  #set to 400 for 0.9 degree stepper
gear_ratio: 50:20
endstop_pin: PG9
position_min: -1.0
position_endstop:805.0
position_max:805.5
homing_speed:100	#max 100 OEM Giga value is 80
homing_retract_dist:10
second_homing_speed:10
homing_positive_dir:true
step_pulse_duration:0.000002

#####################################################################
#   Z Stepper Settings
#####################################################################

[stepper_z]
step_pin: PF11
dir_pin: !PG3
enable_pin: !PG5
microsteps: 16
rotation_distance: 8
gear_ratio: 50:20
full_steps_per_rotation: 200
endstop_pin: PG10 
position_endstop: 11
position_max: 1020
position_min: -15	#OEM Giga value is -12
homing_speed: 10
second_homing_speed: 3
homing_retract_dist: 5
homing_positive_dir:false

[stepper_z1]
step_pin: PG4
dir_pin: !PC1
enable_pin: !PA2
microsteps: 16
rotation_distance: 8
gear_ratio: 50:20
full_steps_per_rotation: 200
endstop_pin: PG11

#####################################################################
#   TMC UART configuration
#####################################################################

#[tmc2209 stepper_x]
#uart_pin: PC4
#run_current: 1.4	#OEM Giga Value is 1.8, this should be 1.4 according to the stepper motor RMS value calcs
#hold_current: 0.8	#OEM Giga Value is 1.0, this should be 0.8 according to the stepper motor hold current calcs	
#interpolate:False

[tmc5160 stepper_x]	# upgraded X axis BTT TMC5160T pro driver OEM Giga has a TMC2209 with a larger heat sink
cs_pin:PC4
spi_bus: spi1
spi_speed:200000
run_current: 2.5
hold_current: 1.5
sense_resistor: 0.075
interpolate:false
#interpolate:True
stealthchop_threshold:0

[tmc5160 stepper_y]	# y axis stepper drive was a Makerbase TMC5160 Pro, this was changed to a BTT TMC5160T pro driver
cs_pin:PD11
spi_bus: spi1
spi_speed:200000
run_current: 2.8
hold_current: 1.7
sense_resistor: 0.075
interpolate:false
#interpolate:True
stealthchop_threshold:0

#[tmc5160 stepper_z]
#cs_pin:PC6
#spi_bus: spi1
#spi_speed:200000
#run_current: 1.4
#hold_current: 1.0
#sense_resistor: 0.075
#interpolate:false
#interpolate:True
#stealthchop_threshold:0

[tmc2209 stepper_z]
uart_pin: PC6
run_current: 1.2
hold_current: 0.8
interpolate:False

#[tmc5160 stepper_z1]
#cs_pin:PC7
#spi_bus: spi1
#spi_speed:200000
#run_current: 1.4
#hold_current: 1.0
#sense_resistor: 0.075
#interpolate:false
#interpolate:True
#stealthchop_threshold:0

[tmc2209 stepper_z1]
uart_pin: PC7
run_current: 1.2
hold_current: 0.8
interpolate:False

[motor_constants moons-ml23hs8l4550-20]	# x axis stepper motor - not exact but similar values - OEM  Giga stated x axis as ldo-42sth60-2004ac with 0.45 resistance, 0.00124 inductance, 1.300 holding torque and a max current of 2.8.
resistance: 0.28
inductance: 0.00103
holding_torque: 1.5
max_current: 5.5
steps_per_revolution: 200

[motor_constants moons-ml23hs0l4350-000]	# y axis stepper motor - not exact but similar values
resistance: 0.56
inductance: 0.0013
holding_torque: 0.82
max_current: 3.5
steps_per_revolution: 200

[motor_constants ldo-42sth60-2004ac]	# Z axis stepper motors - not exact but similar values
resistance: 2.1
inductance: 0.0041
holding_torque: 0.85
max_current: 2
steps_per_revolution: 200

[autotune_tmc stepper_y]
motor: moons-ml23hs8l4550-20
voltage:24

[autotune_tmc stepper_x]
motor: moons-ml23hs0l4350-000
voltage:24

[autotune_tmc stepper_z]
motor: ldo-42sth60-2004ac
voltage:24

[autotune_tmc stepper_z1]
motor: ldo-42sth60-2004ac
voltage:24

#############################################################################
#   Accelerometer Config
############################################################################# 
[resonance_tester]
accel_chip: adxl345
min_freq: 5
max_freq: 90
accel_per_hz: 150
hz_per_sec: 2
probe_points:
    400, 400, 50
    
[gcode_macro Shaper_Calibrate_all]
gcode:
    G28
    SHAPER_CALIBRATE
    
    #############################################################################
    #   Input Shaper Config
    #############################################################################
[input_shaper]
#shaper_freq_x: 66.66    
#shaper_freq_y: 42.05   
#shaper_type_x: mzv
#shaper_type_y: ei

    #####################################################################
    #   Bed Mesh, Probe & Extruder
    #####################################################################
    
[bed_mesh]
horizontal_move_z: 10
speed: 200
# For the mesh dimensions below, the coordinates need to be reachable by the center of the probe. To calculate coordinates that will work, use the formula below:
# mesh x min = position_min_x + greater_of (15mm or x_offset) <--- in this term, only consider the x offset if it is positive, ignore if negative.
# mesh y min = position_min_y + greater_of (15mm or y_offset) <--- in this term, only consider the y offset if it is positive, ignore if negative.
# mesh x max = position_max_x - greater_of (15mm or |x_offset|) <--- in this term, only consider the x offset if it is negative, ignore if positive.
# mesh y max = position_max_y - greater_of (15mm or |y_offset|) <--- in this term, only consider the y offset if it is negative, ignore if positive.
# Example: Consider that you have a 300 x 300 bed with the max x and y positions being 300 and the min being 0. Your probe offsets are -20 for X and 10 for Y
# For mesh x min we ignore the x offset term because it is negative. Therefore mesh x min = 15
# For mesh y min we do not ignore the y offset term because it is positive but it is less than 15 so we use 15. Therefore mesh y min = 15
# For mesh x max we do not ignore the x offset term because it is negative. It is also greater than 15. Therefore mesh x max = 280
# For mesh y max we ignore the y offset term because it is positive but it is less than 15 so we use 15. Therefore mesh y max = 285
# The final result would be mesh_min: 15, 15 mesh_max: 280, 285
mesh_min: 16, 25  # modify these according to the above guide. If the probe cannot reach then you will get a klipper error when trying to scan a bed mesh.
mesh_max: 786, 746 # modify these according to the above guide. If the probe cannot reach then you will get a klipper error when trying to scan a bed mesh.
probe_count: 10, 10
algorithm: bicubic
bicubic_tension:0.2
mesh_pps: 4, 4
fade_start: 1.0
fade_end: 30.0
#scan_overshoot: 8
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

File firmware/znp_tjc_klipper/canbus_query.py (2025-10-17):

#!/usr/bin/env python2
# Tool to query CAN bus uuids
#
# Copyright (C) 2021  Kevin O'Connor <kevin@koconnor.net>
#
# This file may be distributed under the terms of the GNU GPLv3 license.
import sys, os, optparse, time
import can

CANBUS_ID_ADMIN = 0x3f0
CMD_QUERY_UNASSIGNED = 0x00
RESP_NEED_NODEID = 0x20
CMD_SET_KLIPPER_NODEID = 0x01
CMD_SET_KATAPULT_NODEID = 0x11

def query_unassigned(canbus_iface):
    # Open CAN socket
    filters = [{"can_id": CANBUS_ID_ADMIN + 1, "can_mask": 0x7ff,
                "extended": False}]
    bus = can.interface.Bus(channel=canbus_iface, can_filters=filters,
                            bustype='socketcan')
    # Send query
    msg = can.Message(arbitration_id=CANBUS_ID_ADMIN,
                      data=[CMD_QUERY_UNASSIGNED], is_extended_id=False)
    bus.send(msg)
    # Read responses
    found_ids = {}
    uuid_list = []
    start_time = curtime = time.time()
    while 1:
        tdiff = start_time + 2. - curtime
        if tdiff <= 0.:
            break
        msg = bus.recv(tdiff)
        curtime = time.time()
        if (msg is None or msg.arbitration_id != CANBUS_ID_ADMIN + 1
            or msg.dlc < 7 or msg.data[0] != RESP_NEED_NODEID):
            continue
        uuid = sum([v << ((5-i)*8) for i, v in enumerate(msg.data[1:7])])
        cfg_path = set_cfg_path('%012x' % uuid) #Will uuid After converting to a string, it is passed to the judgment function and the corresponding configuration file path is returned.
        sys.stdout.write("%s\n"% (cfg_path))
        if cfg_path:
            modify_config(cfg_path,'%012x' % uuid) #Will uuid Change to the corresponding configuration file
        else:
            uuid_list.append('%012x' % uuid)
        if uuid in found_ids:
            continue
        found_ids[uuid] = 1
        AppNames = {
            CMD_SET_KLIPPER_NODEID: "Klipper",
            CMD_SET_KATAPULT_NODEID: "Katapult"
        }
        app_id = CMD_SET_KLIPPER_NODEID
        if msg.dlc > 7:
            app_id = msg.data[7]
        app_name = AppNames.get(app_id, "Unknown")
        sys.stdout.write("Found canbus_uuid=%012x, Application: %s\n"
                         % (uuid, app_name))
    sys.stdout.write("uuid_list:%s\n" % (uuid_list))
    set_thr_uuid(sorted(uuid_list, key=lambda id: id[-2:]))
    sys.stdout.write("Total %d uuids found\n" % (len(found_ids,)))
def modify_config(file_path, new_uuid):
    if not os.path.exists(file_path):
        sys.stdout.write("File path does not exist: {}".format(file_path))
        return
    with open(file_path, 'r') as file:
        lines = file.readlines()

    with open(file_path, 'w') as file:
        for line in lines:
            if line.startswith('canbus_uuid:'):
                line = 'canbus_uuid: ' + new_uuid + '\n'
            file.write(line)
def set_cfg_path(uuid):
    if uuid[10:12] in ['00', '01', '02', '03']:
        return ""
    else:
        return "/home/biqu/printer_data/config/znp_mcu.cfg"
def set_thr_uuid(uuid_list):
    for i, uuid in enumerate(uuid_list):
        if uuid != '':
            config_path = "/home/biqu/printer_data/config/znp_thr{}.cfg".format(i+1)
            modify_config(config_path, uuid)
            sys.stdout.write("set canbus_uuid:%s into %s\n"% (uuid, config_path))

def main():
    usage = "%prog [options] <can interface>"
    opts = optparse.OptionParser(usage)
    options, args = opts.parse_args()
    if len(args) != 1:
        opts.error("Incorrect number of arguments")
    canbus_iface = args[0]
    query_unassigned(canbus_iface)

if __name__ == '__main__':
    main()

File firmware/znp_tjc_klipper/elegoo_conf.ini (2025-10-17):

# elegoo_conf.ini Version：V1.4-202400420
# Machine type：OrangeStorm Giga

[filament_th_target]
pla                            = 205
abs                            = 240
petg                           = 220
tpu                            = 230
level                          = 140
pid_tmp                        = 170

[filament_tb_target]
pla                            = 60
abs                            = 80
petg                           = 70
tpu                            = 50
level                          = 60

[printer_offset]
z_offset					   = 0
if_use_pe_switch	           = 1
if_auto_save_zoffset           = 1
probe_zoffset                  = 0.0
min_zoffset                     = -11.5
max_zoffset                     = 1050.0

[elegoo_model]
model                          = 3
hwbdv                          = 2.0

[printer]
max_velocity                   = 500
max_accel                      = 20000
max_accel_to_decel             = 10000
machine_use_extruders          = 1
en_copy_extruters_file=0
wlan0_status                   = 1
fila_sensor_status             = 1

[plr_print]
plr_file                       = elegoo
plr_file_estime                = 0
plr_process                    = 0.0
plr_fun_status                 = 1

[z_tilt]
z_tilt_after_home_enable       = 0
z_tile_before_leveling_enable  = 0

[manual_level]
p1_x                           = 30.0
p1_y                           = 30.0
p2_x                           = 30.0
p2_y                           = 210.0
p3_x                           = 30.0
p3_y                           = 385.0
p4_x                           = 385.0
p4_y                           = 385.0
p5_x                           = 385.0
p5_y                           = 210.0
p6_x                           = 385.0
p6_y                           = 30.0
move_speed                     = 5000
probe_up_z                     = 30
probe_speed                    = 10
pre_heat_extruder              = 0
pre_heat_bed                   = 0
z_of_pre_heat                  = 30
x1                             =785.5
y1                             = 63
x2                             = 620.5
y2                             = 63
x3                             = 455.5
y3                             = 63
x4                             = 455.5
y4                             = 228
x5                             = 620.5
y5                             = 203
x6                             = 785.5
y6                             = 228
x7                             = 785.5
y7                             = 393
x8                             = 620.5
y8                             = 393
x9                             = 455.5
y9                             = 393
x10                             = 375
y10                             = 63
x11                             = 210
y11                             = 63
x12                             = 45
y12                             = 63
x13                             = 45
y13                             = 228
x14                             = 210
y14                             = 203
x15                             = 375
y15                             = 228
x16                             = 375
y16                             = 393
x17                             = 210
y17                             = 393
x18                             = 45
y18                             = 393
x19                             = 375
y19                             = 473
x20                             = 210
y20                             = 473
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

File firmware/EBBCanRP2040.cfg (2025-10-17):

###########################################################################################
# EBB Canbus RP2040
###########################################################################################

[mcu EBBCan] 
canbus_uuid: xxxxxxxxxxxx     # put your Katapult/Klipper CANBus ID here
canbus_interface: can0

[mcu eddy]
canbus_uuid: xxxxxxxxxxxx     # put your Katapult/Klipper CANBus ID here
canbus_interface: can0

[temperature_sensor EBB_NTC]     # Temperature sensor on the EBB SB2209 RP2040. handy for monitoring the extruder motor ambient temperature
sensor_type: Generic 3950
sensor_pin: EBBCan:gpio28
min_temp: -120
max_temp: 100

[adxl345]       # Accelerometer sensor for Klipper Shapping and speed calibration for the stepper motors.
cs_pin: EBBCan:gpio1
spi_software_sclk_pin: EBBCan:gpio2
spi_software_mosi_pin: EBBCan:gpio0
spi_software_miso_pin: EBBCan:gpio3
axes_map: z,-y,x

[extruder]
step_pin: EBBCan:gpio18
dir_pin: EBBCan:gpio19
enable_pin: !EBBCan:gpio17
microsteps: 16
rotation_distance: 40
gear_ratio: 9:1
#nozzle_diameter: 0.400    # moved to printer.cfg so that Klipper can overwrite the values
#filament_diameter: 1.750
#heater_pin: EBBCan:gpio7
sensor_type: MAX31865    # Sensor for the PT1000
sensor_pin: EBBCan:gpio9
#spi_bus: spi1
spi_software_sclk_pin: EBBCan:gpio10    #spi pins used for the extruder stepper, SB EBB2209 has SPI pins out so it seems the hardware is only comfortable when the spi pins are designated even though TMC2209 stepper drivers can't communicate in spi 
spi_software_mosi_pin: EBBCan:gpio8
spi_software_miso_pin: EBBCan:gpio11
rtd_nominal_r: 1000    # required by the PT1000
rtd_reference_r: 4300    # required by the PT1000
rtd_num_of_wires: 2    # required by the PT1000
rtd_use_50Hz_filter: True
max_extrude_cross_section: 5
#control: pid    # moved to printer.cfg so that PID_CALIBRATE can overwrite the values
#pid_Kp: 33.093
#pid_Ki: 1.808
#pid_Kd: 151.397
min_temp: 0
max_temp: 350 
max_extrude_only_distance: 400
step_pulse_duration:0.000002
instantaneous_corner_velocity: 2.5
#sensor_type: EPCOS 100K B57560G104F    # sensor for other thermistor type like the PT100
#sensor_pin: EBBCan:gpio27 

[verify_heater extruder]
max_error: 120
check_gain_time:20
hysteresis: 5
heating_gain: 2

[tmc2209 extruder]
uart_pin: EBBCan:gpio20
run_current: 0.7    # normally set at around 0.6-0.8. find the right run current for your pancake stepper by taking the RMS current or by finding the peak current and multiplying by 0.707
sense_resistor: 0.11
stealthchop_threshold: 0
interpolate: false
driver_TBL: 0
driver_HEND: 6
driver_HSTRT: 7
driver_TOFF: 4

[filament_switch_sensor switch_sensor]    # If you're using the BTT SMART filament sensor using the probe port on the SB EBB2209
switch_pin: EBBCan:gpio21
pause_on_runout: False
runout_gcode:
  PAUSE ## [pause_resume] is required in printer.cfg
  M117 Filament has runout!
insert_gcode:
  M117 Filament is primed!

[filament_motion_sensor encoder_sensor]    # If you're using the BTT SMART filament sensor using the probe port on the SB EBB2209
switch_pin: EBBCan:gpio22 
detection_length:2.88
extruder: extruder
pause_on_runout: False
runout_gcode:
  PAUSE ## [pause_resume is required in printer.cfg
  M117 Filament Clogged! 

[heater_fan fan]    # Heat break fan
pin: EBBCan:gpio14
max_power: 1.0
shutdown_speed: 0
cycle_time: 0.010
kick_start_time: 0.100
heater: extruder
heater_temp: 10.0
fan_speed: 1.0
off_below: 0

[fan]    # part cooling fan or blower fan, directly controlled by your inputs from orca slicer or whatever slicer program that enables part cooling
pin: EBBCan:gpio13
max_power: 1.0
shutdown_speed: 0
cycle_time: 0.010
hardware_pwm: False
kick_start_time: 0.500
#heater: extruder
#heater_temp: 50.0
#fan_speed: 1.0
#off_below: 0


[neopixel hotend_rgb]    # Neopixel RGB lights around the hotend, make sure the chain count and color order is right for your RGB version
pin: EBBCan:gpio16
chain_count: 3
color_order: GRBW 

[delayed_gcode hotend_rgb]    # this is to programe the rgb to change color according to the temperature of the hotend, green for cool, red for hot.
initial_duration: 5.
gcode:
    {% if printer.extruder.temperature > 50 %}
        SET_LED LED=hotend_rgb RED=1 GREEN=0 BLUE=0 INDEX=1 TRANSMIT=1
        SET_LED LED=hotend_rgb RED=1 GREEN=0 BLUE=0 INDEX=2 TRANSMIT=1
        SET_LED LED=hotend_rgb RED=1 GREEN=0 BLUE=0 INDEX=3 TRANSMIT=1
    {% else %}
        SET_LED LED=hotend_rgb RED=0 GREEN=1 BLUE=0 INDEX=1 TRANSMIT=1
        SET_LED LED=hotend_rgb RED=0 GREEN=1 BLUE=0 INDEX=2 TRANSMIT=1
        SET_LED LED=hotend_rgb RED=0 GREEN=1 BLUE=0 INDEX=3 TRANSMIT=1
    {% endif %}
     UPDATE_DELAYED_GCODE ID=hotend_rgb DURATION=5

#[bltouch]     # Currently being used by the filament sensor
#sensor_pin: ^EBBCan:gpio21
#control_pin: EBBCan:gpio22

## NPN and PNP proximity switch types can be set by jumper    # Currently not being used but you can reuse the Orangestorm Giga PNP Probe if you wish and plug it into the NPN ad PNP port on the SB EBB2209
#[probe]
#pin: ^EBBCan:gpio6

[temperature_sensor btt_eddy_mcu]    # Temperature sensor on the BTT Eddy, handly if you want to check on the heat around your hotend to ensure your plastic components aren't melting.
sensor_type: temperature_mcu # Sets the type of sensor for Klipper to read
sensor_mcu: eddy # Sets the MCU of the eddy probe tempereature sensor
min_temp: 10 # Sets the minimum tempereature for eddys tempereature sensor to operate
max_temp: 100 # Sets the maximum tempereature for eddys tempereature sensor to operate

[probe_eddy_current btt_eddy]    # Eddy current settings. pretty much the same for every model
sensor_type: ldc1612
z_offset: 2.5
#i2c_address:
i2c_mcu: eddy  # This value is good for the Eddy USB but would need to be adjusted for the Eddy Coil according to the MCU you have used.
i2c_bus: i2c0f # This value is good for the Eddy USB but would need to be adjusted for the Eddy Coil according to the I2C bus you have used.
# Measure the offsets below using the method described here: https://www.klipper3d.org/Probe_Calibrate.html#calibrating-probe-x-and-y-offsets
# For a standard Voron stealthburner X carriage mount there should be no need to change the defaults below.
x_offset: 0
y_offset: -21
#reg_drive_current: 15    # run an eddy current calibration to make sure you have the right value but most of the time its 15.

#[bed_mesh]    # Normally in printer.cfg so that the bed mesh values can be overwritten when you run a bed mesh. Copy and paste this section there.
#horizontal_move_z: 10
#speed: 200
# For the mesh dimensions below, the coordinates need to be reachable by the center of the probe. To calculate coordinates that will work, use the formula below:
# mesh x min = position_min_x + greater_of (15mm or x_offset) <--- in this term, only consider the x offset if it is positive, ignore if negative.
# mesh y min = position_min_y + greater_of (15mm or y_offset) <--- in this term, only consider the y offset if it is positive, ignore if negative.
# mesh x max = position_max_x - greater_of (15mm or |x_offset|) <--- in this term, only consider the x offset if it is negative, ignore if positive.
# mesh y max = position_max_y - greater_of (15mm or |y_offset|) <--- in this term, only consider the y offset if it is negative, ignore if positive.
# Example: Consider that you have a 300 x 300 bed with the max x and y positions being 300 and the min being 0. Your probe offsets are -20 for X and 10 for Y
# For mesh x min we ignore the x offset term because it is negative. Therefore mesh x min = 15
# For mesh y min we do not ignore the y offset term because it is positive but it is less than 15 so we use 15. Therefore mesh y min = 15
# For mesh x max we do not ignore the x offset term because it is negative. It is also greater than 15. Therefore mesh x max = 280
# For mesh y max we ignore the y offset term because it is positive but it is less than 15 so we use 15. Therefore mesh y max = 285
# The final result would be mesh_min: 15, 15 mesh_max: 280, 285
#mesh_min: 16, 25  # modify these according to the above guide. If the probe cannot reach then you will get a klipper error when trying to scan a bed mesh.
#mesh_max: 786, 746 # modify these according to the above guide. If the probe cannot reach then you will get a klipper error when trying to scan a bed mesh.
#probe_count: 10, 10
#algorithm: bicubic
#bicubic_tension:0.2
#mesh_pps: 4, 4
#fade_start: 1.0
#fade_end: 30.0
#scan_overshoot: 8
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

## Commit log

2025-08-20 Orca Profiles for Jcw_Giga
    These Orca Profiles include gcode for singular bed heating depending on which bed the print is on, it also includes BTT EDDY bed leveling.
    Please be aware of your Z offset as different nozzles and print heads can vary and you may end up grinding your nozzle into the print bed.
    To allow for this, always run a Auto Probe Calibrate whenever changing the head or nozzles.
2025-08-20 3D Print Files
    These include 3D printed upgrades like the print head adapter for the StealthBurner. They also include different hotends such as the Dragon Ace, Bambulabs hotends and Revo hotends.
    [Bed standoffs.3mf, Bush for Z axis Calibration.stp, Nema17 to Nema23 adapter.stl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]
2025-08-20 Jcw-GigaVoron Firmware
    Jcw-GigaVoron Firmware please install according to the authors specifications. Some files here are simply to show that they have been included.
    [EBBCan.cfg, EBBCanRP2040.cfg, KAMP_Settings.cfg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]
2025-08-20 CANBus board Flashing pdf's
2025-08-28 Chain Bracket and breakout board weight reduction
    Simple but effective weight reduction of the Bracket holding the cable chain and breakout board for the print heads. This also acts as the X end stop so ensure any printed parts are rock solid. Proto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
    [Cable Chain bracket V2.stp]
2025-08-28 Corner Bracket with quick release hood Pins socket
    Modified Corner Bracket with quick release hood pin socket for quick release enclosure. If Possible, this part should be machined steel. Failing that, print in PPS CF or a composite that can handle heat, high tensile forces and have a low moisture absorption rate. Some analysis conducted on electro plated components in Cobalt Nickel.
    [Corner brace with engine mount.stp]
2025-10-14 Printer head carriage bracket
    Printer head carriage bracket - when the aluminum threads wear out on the cheap 5051 aluminum bracket or when the bracket gets bent due to print failure.
    [giga print head carriage.stp]
2025-10-17 Update EBBCan.cfg
    Modified config for the printhead with some observed necessary config.
    [EBBCan.cfg]
2025-10-17 Update EBBCanRP2040.cfg
    Updated config to include some observed necessary changes
    [EBBCanRP2040.cfg]
2025-10-17 Update printer.cfg
    updated printer.cfg for install on a BTT pi v1.2
    [printer.cfg]
2025-10-17 Elegoo Orangestorm Giga OEM Config's
    [fluidd.cfg, plr.cfg, printer.cfg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]
2025-10-17 Elegoo Orangestorm Giga TJC screen Klipper files
    [1_extruder.cfg, 2_extruder.cfg, 3_extruder.cfg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]
2025-10-17 Elegoo Orangestorm giga TJC screen klipper file
2025-10-17 Orca Printer Profiles
2025-10-17 OEM 10.1" TJC screen integration with Klipper v13
2025-10-20 Create Install guide raspberry pi.md
2025-10-20 Update Install guide raspberry pi.md
2025-10-21 Dragon ACE extended print head models
    [Dragon Ace with extension.stl, dragon ace with extension Bottom back.stl, stealth burner ace with extension bottom front.stl]
2025-10-21 Elegoo Orangestorm Giga extruder parts
    [4010 Axial Fan.stp, 5015 Fan.stp, Elegoo Nozzle.stp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]
2025-10-21 Elegoo Orangestorm Giga Stock Printer Head Parts
    [4010 Axial Fan.stp, 5015 Fan.stp, Elegoo Nozzle.stp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]
2025-10-21 Dragon Ace with the extender 3D Print Files
    [Dragon ACE SB with Extension Back.stl, Dragon ACE SB with Extension Front.stl, Dragon Ace SB with Extension Face.stl]
2025-10-21 3D Print File Bambulabs nozzle SB Adapter
    [BambuLabs SB Adapter.stl, BambuLabs SB Back.stl, Bambulab SB Front.stl]
2025-10-21 3D Print File - E3D Revo SB adapter
    [E3D Revo SB Back.stl, E3D Revo SB Front.stl]
2025-10-21 3D Print File - SB Galileo V2
    [SB Galileo Base Hinge Retainer.stl, SB Galileo Extruder Bearing Retainer.stl, SB Galileo Extruder Gear Housing.stl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]
2025-10-21 3D Print File - Dragon Ace SB
    [Dragon ACE SB Back.stl, Dragon ACE SB Front.stl]
2025-10-21 3D Print File - OG Dragon SB Adapter
    [Dragon SB Back.stl, Dragon SB Front.stl]
2025-10-21 3D Print File - Stealth Burner Components
    [KNOMI 2 Retaining Plate.stl, SB Electronics Shroud.stl, SB LED Housing.stl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]
2025-10-21 Jcw SB Face Plate
    [Jcw Drafting Stealth Burner Face.stl]
2025-10-22 3D Print Files - Modified Giga Components
    Modified Giga Components including Brackets, Leveling bushes, and more.
    [Bed Leveling Bushes.stl, Giga Extruder Canbus cable chain bracket.stl, Giga Extruder Linear Rail Plate.stl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]
